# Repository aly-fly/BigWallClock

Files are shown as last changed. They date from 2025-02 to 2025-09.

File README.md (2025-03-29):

# Big Wall Clock
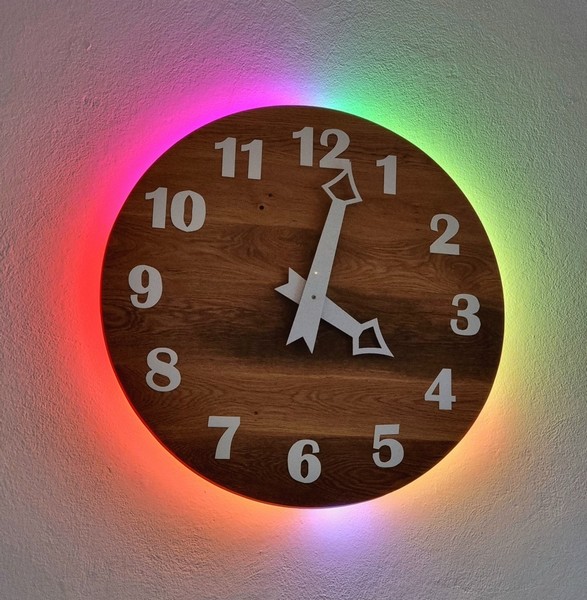
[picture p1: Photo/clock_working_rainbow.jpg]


### Story time.
_I was walking through the hardware store with my wife. High up on the wall was a huge, beautiful wooden clock. Like one meter diameter. Price tag was also pretty high. I said "I can make one like this." My brain immediately started adding features and making improvements. When the permission was given to kick-off the project, I was happy!_

## What we need

* Wooden plate
* Mechanism
* Feedback device
* Motor and driver
* Controller
* Clock hands and numbers
* Power supply

### Wooden plate
If you don't have a relative or friend that has a woodworking shop, best next option is a local furniture producer. Or recycle some other furniture with nice looking patterns.

### Mechanism
Clock with 1 meter diameter needs big and heavy clock hands. Standard off-the-shelf driving mechanism is not strong enough, and it also doesn't offer much challenges. 
Having a 3D printer in my workshop and with lots of initiative to learn mechanical design, I downloaded Autodesk Fusion Personal and started learning. Produced design is not optimal, but works pretty well. For the next iteration (if it ever comes up) one more gear after the motor is needed to increase the torque. Everything is printed from PLA, as it is hard enough so that gears should last quite some time. PETG was an alternative, as it has better dimensional tolerances and better endurance, but for now it was not needed. 

Images: ´3D_Design >> images´

Complete 3D project (Step file): ´3D_Design >> project´

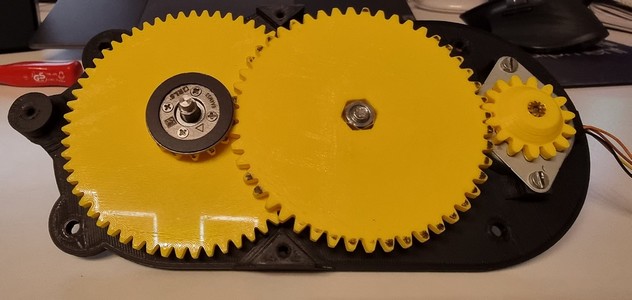
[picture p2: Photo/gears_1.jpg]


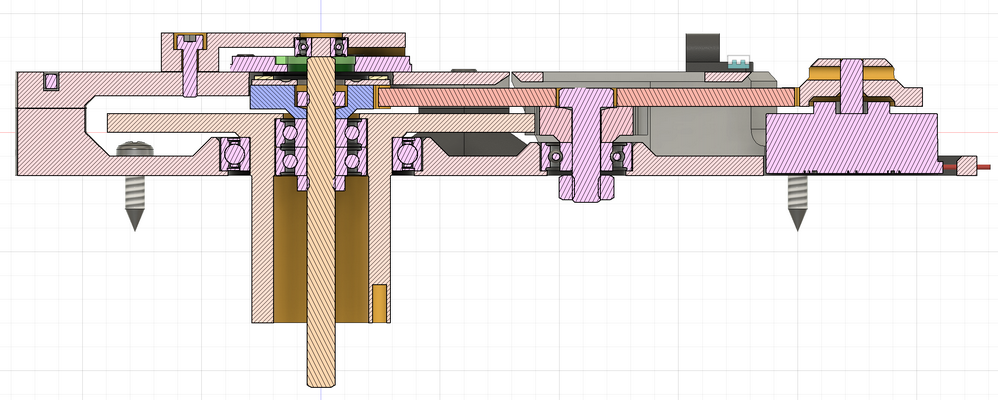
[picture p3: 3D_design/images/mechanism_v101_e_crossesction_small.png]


### Feedback device
Main idea is that clock adjusts itself to the correct time, and also takes care of the Daylight Savings time changes. For this it is required to know exact position of the clock hands. As an engineer developing the rotary encoders, my first thought was which part from our portfolio would fit. [AksIM-2](https://www.rls.si/eng/aksim-2-off-axis-rotary-absolute-encoder) with 29 mm diameter was a perfect fit. With 17-bit resolution this gives more than 2000 counts between two neighboring minute marks on the clock face. A bit too much isn't it :) But this can be used to make a very smooth and precise time-keeping. As encoder has RS422 differential output, a line-driver is required to convert signals to 3.3V LVTTL for the processor.

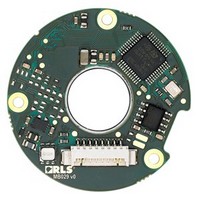
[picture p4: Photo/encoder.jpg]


### Motor and driver
With very low space available, the only motor that would fit was some thin stepper. AliExpress delivered again. Two variants were ordered, first one with 90 steps didn't have enough torque, so slightly thicker motor with better precision and better build quality was a good candidate. [0.9 Degree Mini 36mm Round Thin Stepper Motor](https://www.aliexpress.com/item/1005008263498118.html)

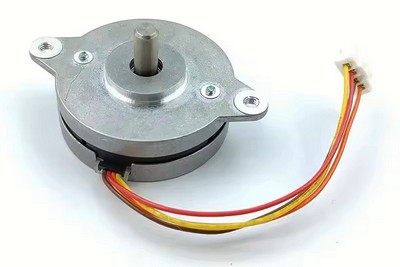
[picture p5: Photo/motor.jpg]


Having a stepper driver at hand from some other project was beneficial. ST-Spin family has some really great devices. [PowerStep01](https://www.st.com/en/motor-drivers/powerstep01.html) chip is way too powerful for what is needed here, but pure sine wave driver with 128-microstepping and quiet voltage mode really makes difference in this project.

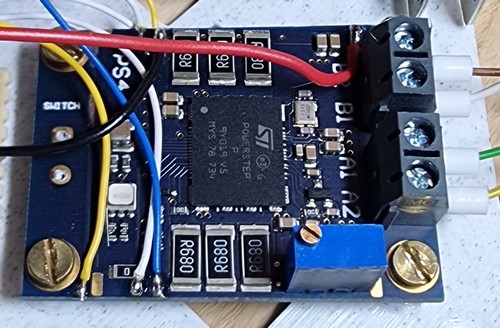
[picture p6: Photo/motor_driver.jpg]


### Controller
The programming work starts here. We need something easy to use, powerful, with lots of peripherals and of course Wi-Fi connectivity. ESP32 series is an easy choice. 
* Wi-Fi is used to get current time from the NTP server
* MQTT client talks to the Home Assistant
* UART polls data from the encoder
* SPI Sends commands to the motor driver
* ADC reads the temperature sensor of the motor
* RMT peripheral controls the addressable LED strip
* Flash filesystem is used to store system messages for later review

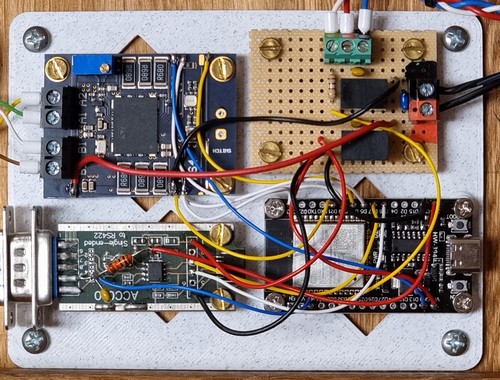
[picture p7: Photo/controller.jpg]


### Clock hands and numbers
Everything designed in Autodesk Fusion Personal and printed from PLA or PETG. 

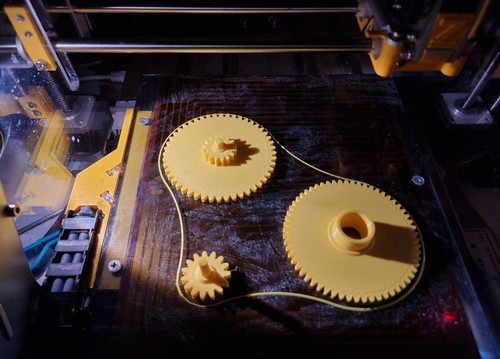
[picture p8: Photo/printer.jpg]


### LED strip
120 LEDs is a nice number to have one pixel per minute plus one in between. 60 LEDs per meter is a good choice for nice and uniform colors. The Chinese guys [delivered again](https://www.aliexpress.com/item/1005006838558445.html). LED strip is mounted using custom brackets, as can be seen in the folder ´3D_Design >> images´

### Power supply
Such a project can't be battery powered. A standard 24 V, 1 A, wall-plug supply works well. 24 V is for the motor driver. 
- Traco power [TSR 1-2450](https://www.tracopower.com/int/model/tsr-1-2450) powers the ESP32 board and encoder (1A limit).
- Traco power [TSR 3-24150](https://www.tracopower.com/int/series/tsr-3) powers the LED strip (3A limit).

## Everything mounted and tested
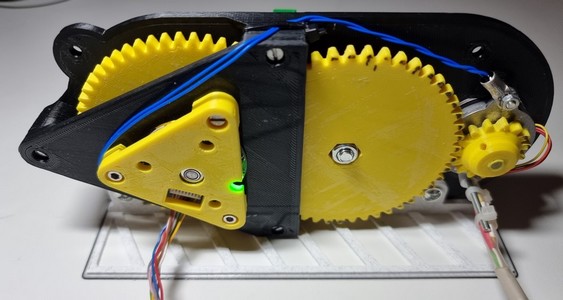
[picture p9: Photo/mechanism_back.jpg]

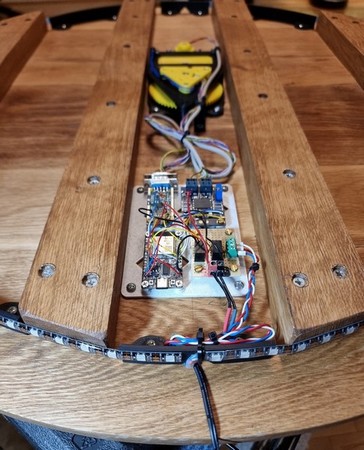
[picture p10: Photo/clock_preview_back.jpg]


### And final step is HA integration
And then the family starts enjoying the new decoration in the house.

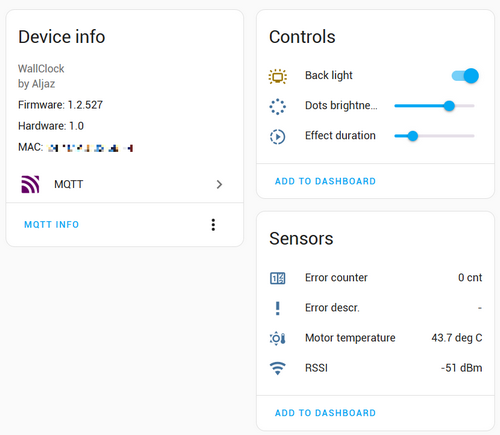
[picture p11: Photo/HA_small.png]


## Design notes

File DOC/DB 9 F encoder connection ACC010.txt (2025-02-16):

DB 9 female

  pin 1
+----------------------------+
 \  00  grn  yel  gry  brn  /
  \   red  blu  pnk  wht   /
   +----------------------+

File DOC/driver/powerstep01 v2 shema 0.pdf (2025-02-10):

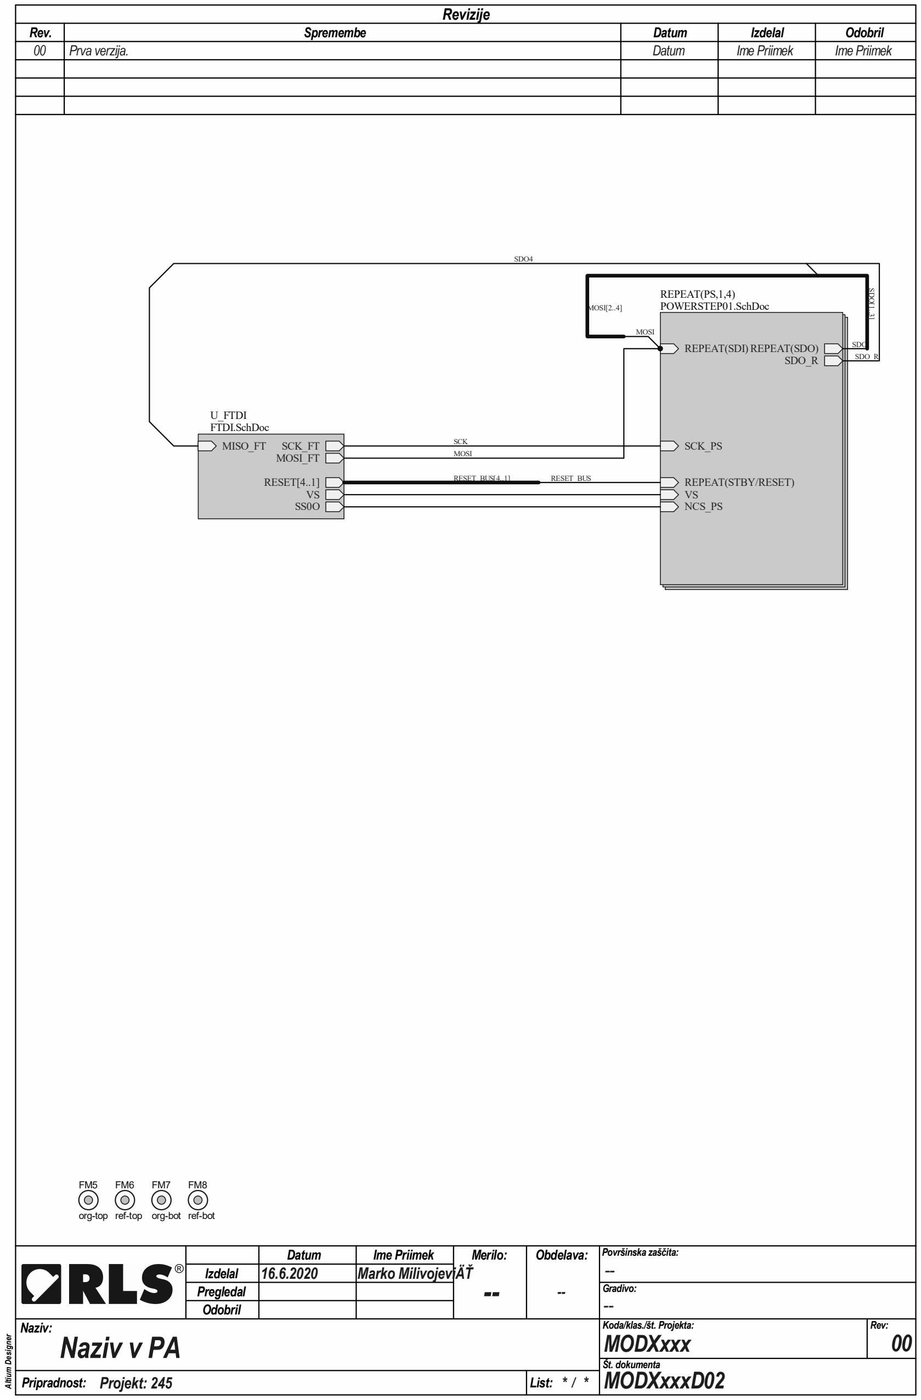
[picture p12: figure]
Rev.; Spremembe; Datum; Izdelal; Odobril; Revizije Altium Designer; 16.6.2020 Marko MilivojeviÄŤ; Pregledal; Gradivo: --; Pripradnost:; List:; Št. dokumenta; Projekt: 245; MODXxxxD02; org-top; ref-top; org-bot; ref-bot; RESET_BUS[4..1]; RESET_BUS; MOSI; SCK; SCK_PS; REPEAT(SDI)REPEAT(SDO); REPEAT(STBY/RESET) VS NCS_PS; SDO_R; REPEAT(PS,1,4); MOSI[2..4]; POWERSTEP01.SchDoc; SDO; SCK_FT MOSI_FT; MISO_FT; RESET[4..1]; U_FTDI FTDI.SchDoc; SDO4; SDO[1..3]

00 | Prva verzija. | Datum | Ime Priimek | Ime Priimek
| | Datum | Ime Priimek | Merilo: -- | Obdelava: -- | Površinska zaščita: --
Naziv: Naziv v PA | Koda/klas./št. Projekta: MODXxxx | Rev: 00

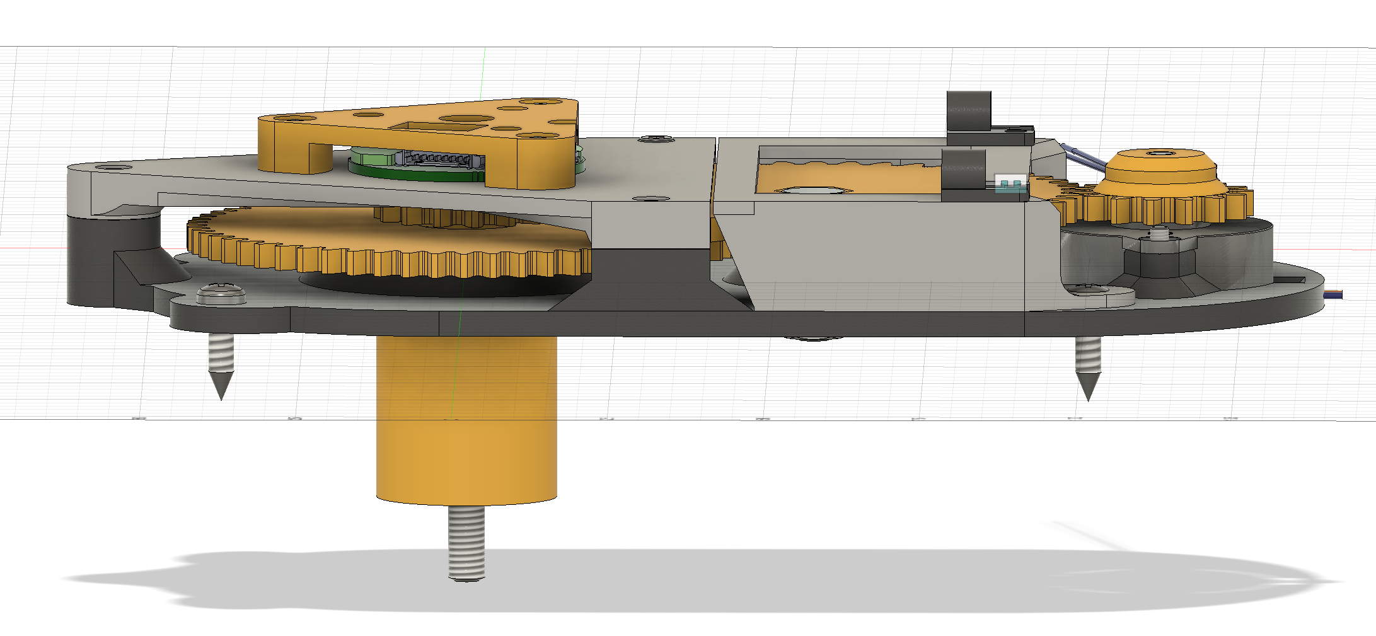
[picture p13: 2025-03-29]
3D_design/images/mechanism_v101_c.png

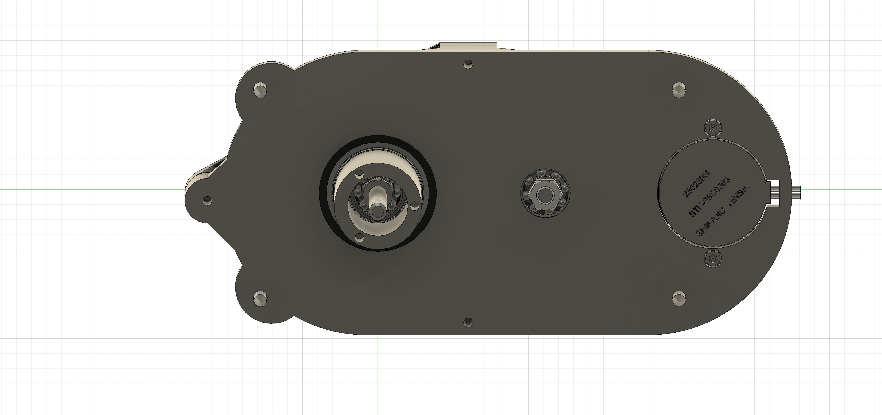
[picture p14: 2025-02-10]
3D_design/DOC/pogonski mehanizem v96 e.png

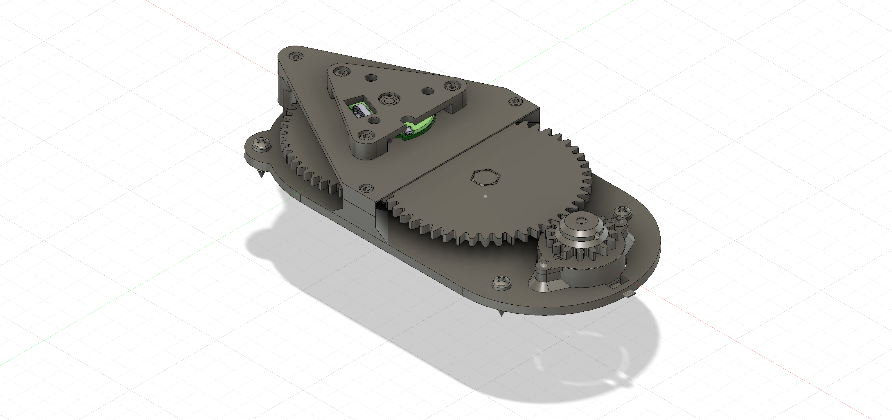
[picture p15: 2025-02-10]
3D_design/DOC/pogonski mehanizem v96 b.png

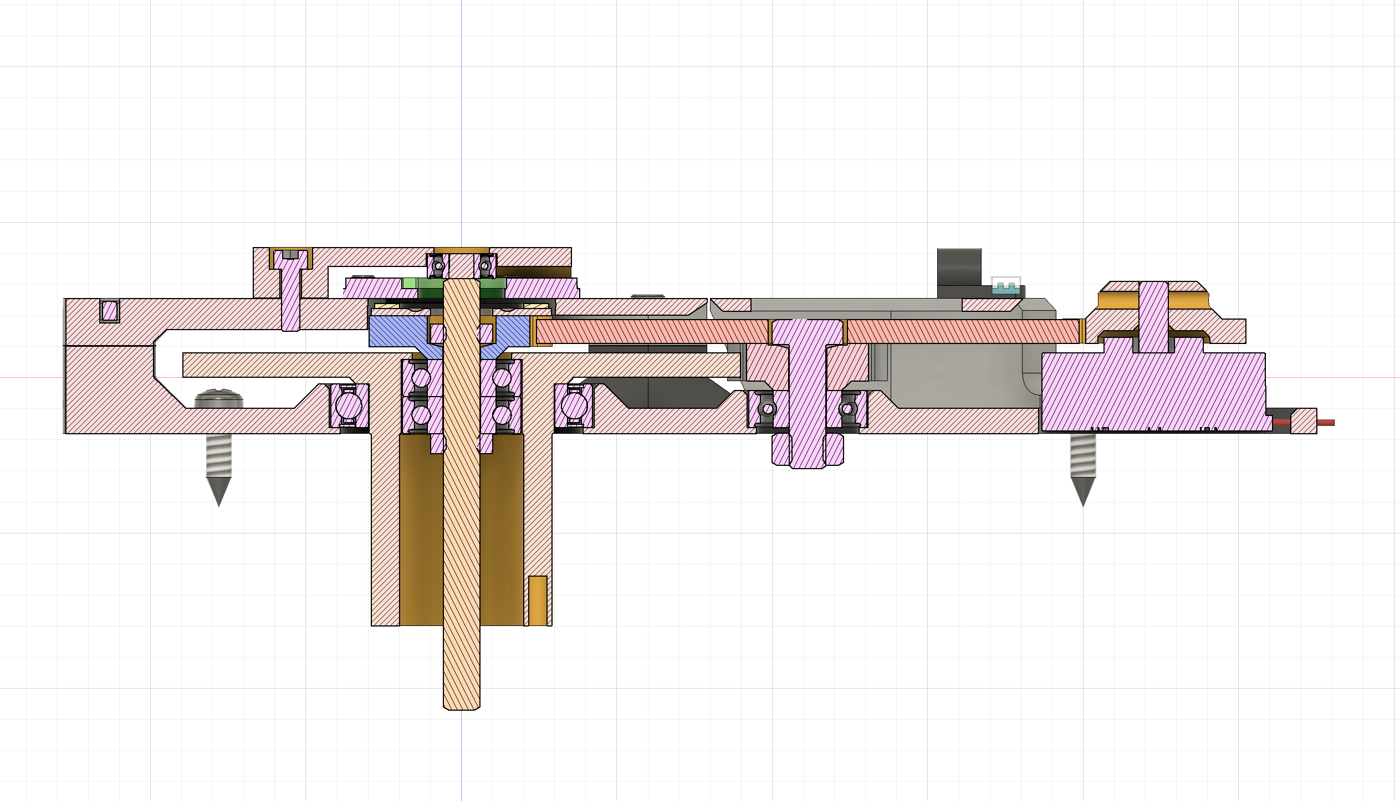
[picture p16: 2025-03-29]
3D_design/images/mechanism_v101_e_crossesction.png

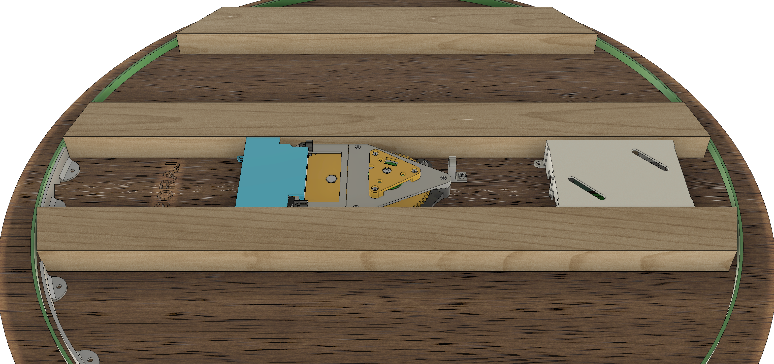
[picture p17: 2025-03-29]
3D_design/images/back_view_1.png

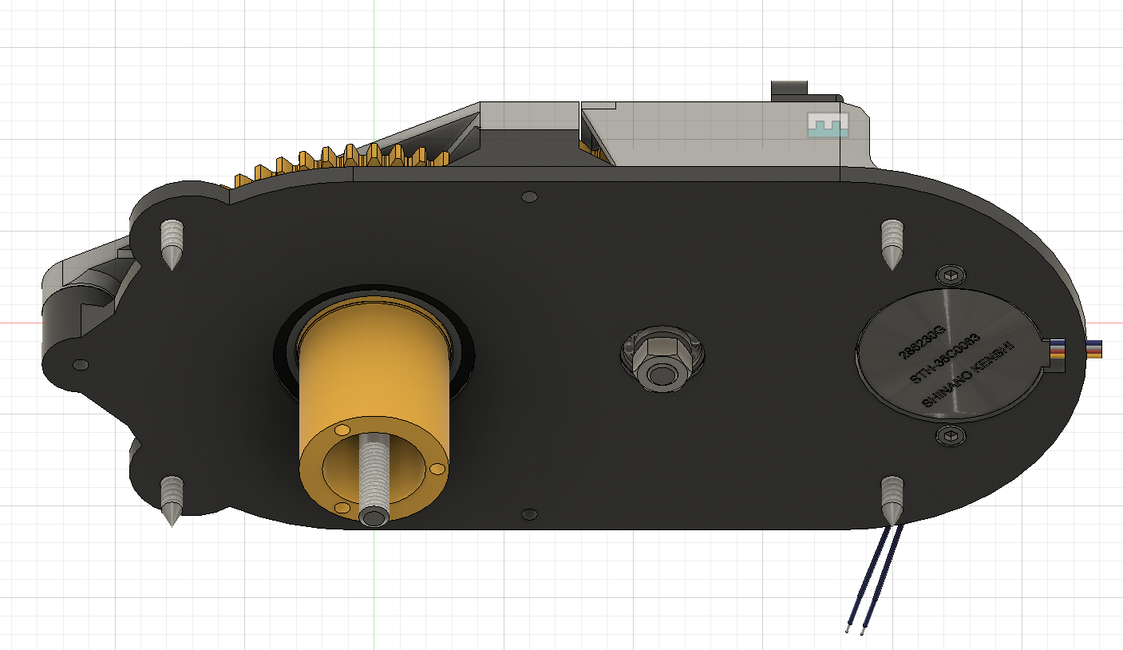
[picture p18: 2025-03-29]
3D_design/images/mechanism_v101_b.png

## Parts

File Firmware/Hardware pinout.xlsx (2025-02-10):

No. | Name | Type | GPIO | True GPIO | RTC_GPIO | ADC | TOUCH | DAC | I2C | VSPI | HSPI | SD/SDIO/MMC Host Controller | UART | Parallel QSPI | JTAG | SDIO Slave | Ethernet | Comment | USED
25 | IO00 | I/O | GPIO00 | No | RTC_GPIO11 | ADC2_CH01 | TOUCH1 |  |  |  |  |  |  |  |  |  | EMAC_TX_CLK | Low for flashing | Flashing
35 | TXD0 | I/O | GPIO01 | No |  |  |  |  |  |  |  |  | U0TXD |  |  |  | EMAC_RXD2 | Bootloader | Flashing, debug
24 | IO02 | I/O | GPIO02 | No | RTC_GPIO12 | ADC2_CH02 | TOUCH2 |  |  |  |  | HS2_DATA0 |  | HSPIWP |  |  |  | Floating or low for flashing | Flashing
34 | RXD0 | I/O | GPIO03 | No |  |  |  |  |  |  |  |  | U0RXD |  |  |  |  | Bootloader | Flashing, debug
26 | IO04 | I/O | GPIO04 |  | RTC_GPIO10 | ADC2_CH0 | TOUCH0 |  |  |  |  | HS2_DATA1 |  | HSPIHD |  |  | EMAC_TX_ER
29 | IO05 | I/O | GPIO05 |  |  |  |  |  |  | SS/CS |  | HS1_DATA6 |  | VSPICS0 |  |  | EMAC_RX_CLK |  | PowerStep01 motor driver VSPI
20 | SCK/CLK* | I/O | GPIO06 | No | UNUSABLE !!! (Flash memory) |  |  |  |  |  |  | HS1_CLK | U1CTS | SPICLK |  | SD_CLK
21 | SDO/SD0* | I/O | GPIO07 | No | UNUSABLE !!! (Flash memory) |  |  |  |  |  |  | HS1_DATA0 | U2RTS | SPIQ |  | SD_DATA0
22 | SDI/SD1* | I/O | GPIO08 | No | UNUSABLE !!! (Flash memory) |  |  |  |  |  |  | HS1_DATA1 | U2CTS | SPID |  | SD_DATA1
17 | SHD/SD2* | I/O | GPIO09 | No | UNUSABLE !!! (Flash memory) |  |  |  |  |  |  | HS1_DATA2 | U1RXD | SPIHD |  | SD_DATA2
18 | SWP/SD3* | I/O | GPIO10 | No | UNUSABLE !!! (Flash memory) |  |  |  |  |  |  | HS1_DATA3 | U1TXD | SPIWP |  | SD_DATA3
19 | SCS/CMD* | I/O | GPIO11 | No | UNUSABLE !!! (Flash memory) |  |  |  |  |  |  | HS1_CMD | U1RTS | SPICS0
14 | IO12 | I/O | GPIO12 | No | RTC_GPIO15 | ADC2_CH05 | TOUCH5 |  |  |  |  | HS2_DATA2 |  | HSPIQ | MTDI |  | EMAC_TXD3 | LOW during boot!
16 | IO13 | I/O | GPIO13 |  | RTC_GPIO14 | ADC2_CH04 | TOUCH4 |  |  |  |  | HS2_DATA3 |  | HSPID | MTCK |  | EMAC_RX_ER
13 | IO14 | I/O | GPIO14 |  | RTC_GPIO16 | ADC2_CH06 | TOUCH6 |  |  |  |  | HS2_CLK |  | HSPICLK | MTMS |  | EMAC_TXD2
23 | IO15 | I/O | GPIO15 |  | RTC_GPIO13 | ADC2_CH03 | TOUCH3 |  |  |  |  | HS2_CMD |  | HSPICS0 | MTDO |  | EMAC_RXD3 | Prevents startup log
27 | IO16 | I/O | GPIO16 |  |  |  |  |  |  |  |  | HS1_DATA4 | U2RXD |  |  |  | EMAC_CLK_OUT |  | Encoder DATA
28 | IO17 | I/O | GPIO17 |  |  |  |  |  |  |  |  | HS1_DATA5 | U2TXD |  |  |  | EMAC_CLK_OUT_180 |  | Encoder CMD
30 | IO18 | I/O | GPIO18 |  |  |  |  |  |  | SCLK |  | HS1_DATA7 |  | VSPICLK |  |  |  |  | PowerStep01 motor driver VSPI
31 | IO19 | I/O | GPIO19 |  |  |  |  |  |  | MISO |  |  | U0CTS | VSPIQ |  |  | EMAC_TXD0 |  | PowerStep01 motor driver VSPI
33 | IO21 | I/O | GPIO21 |  |  |  |  |  | SDA1 |  |  |  |  | VSPIHD |  |  | EMAC_TX_EN |  | PowerStep01 motor driver nReset
36 | IO22 | I/O | GPIO22 |  |  |  |  |  | SCL1 |  |  |  | U0RTS | VSPIWP |  |  | EMAC_TXD1
37 | IO23 | I/O | GPIO23 |  |  |  |  |  |  | MOSI |  | HS1_STROBE |  | VSPID |  |  |  |  | PowerStep01 motor driver VSPI
10 | IO25 | I/O | GPIO25 |  | RTC_GPIO06 | ADC2_CH08 |  | DAC_1 |  |  |  |  |  |  |  |  | EMAC_RXD0
11 | IO26 | I/O | GPIO26 |  | RTC_GPIO07 | ADC2_CH09 |  | DAC_2 |  |  |  |  |  |  |  |  | EMAC_RXD1
12 | IO27 | I/O | GPIO27 |  | RTC_GPIO17 | ADC2_CH07 | TOUCH7 |  |  |  |  |  |  |  |  |  | EMAC_RX_DV
8 | IO32 | I/O | GPIO32 |  | RTC_GPIO09 | ADC1_CH04 | TOUCH9 |  |  |  |  |  |  |  |  |  |  | XTAL_32K_P (32.768kHz oscillator input) | LED WS2812 data
9 | IO33 | I/O | GPIO33 |  | RTC_GPIO08 | ADC1_CH05 | TOUCH8 |  |  |  |  |  |  |  |  |  |  | XTAL_32K_N (32.768kHz oscillator outut)
6 | IO34 | I | GPIO34 | No | RTC_GPIO04 | ADC1_CH06 |  |  |  |  |  |  |  |  |  |  |  | No internal pullup
7 | IO35 | I | GPIO35 | No | RTC_GPIO05 | ADC1_CH07 |  |  |  |  |  |  |  |  |  |  |  | No internal pullup
4 | SENSOR_VP | I | GPIO36 | No | RTC_GPIO00 | ADC1_CH0 |  |  |  |  |  |  |  |  |  |  |  | No internal pullup
5 | SENSOR_VN | I | GPIO39 | No | RTC_GPIO03 | ADC1_CH03 |  |  |  |  |  |  |  |  |  |  |  | No internal pullup | NTC motor temperature sensor
1 | GND | PWR
2 | 3V3 | PWR
3 | EN | I
15 | GND | PWR
32 | NC | NC
38 | GND | PWR

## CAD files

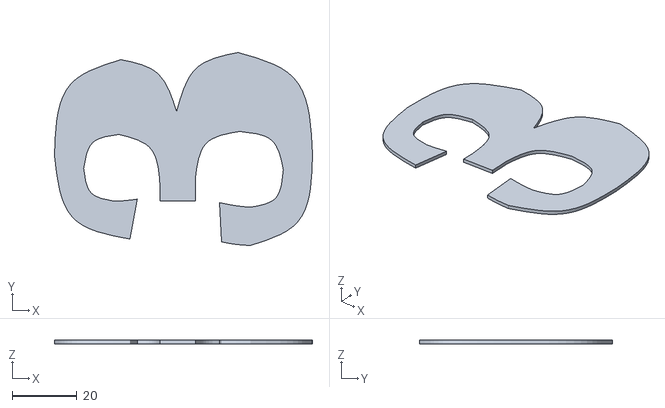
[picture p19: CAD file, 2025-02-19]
3D_design/build/Britannic Bold 77/3.stl
79.6 x 59.6 x 1.10

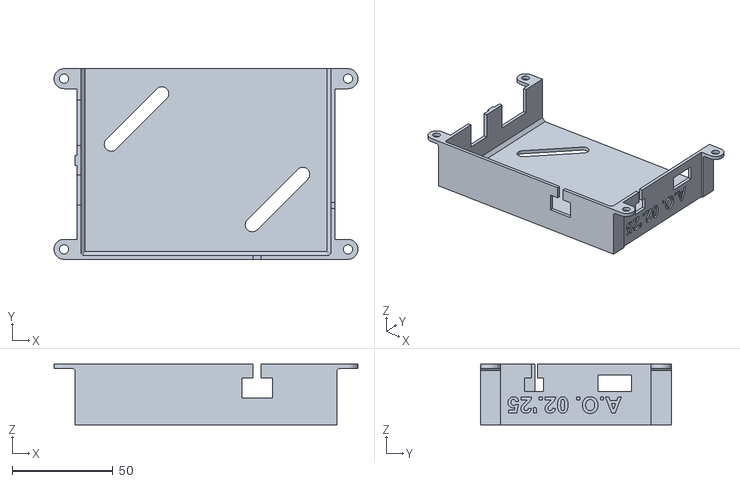
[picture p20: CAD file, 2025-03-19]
3D_design/build/pokrov elektronike 2.stl
150.9 x 94.7 x 30.1

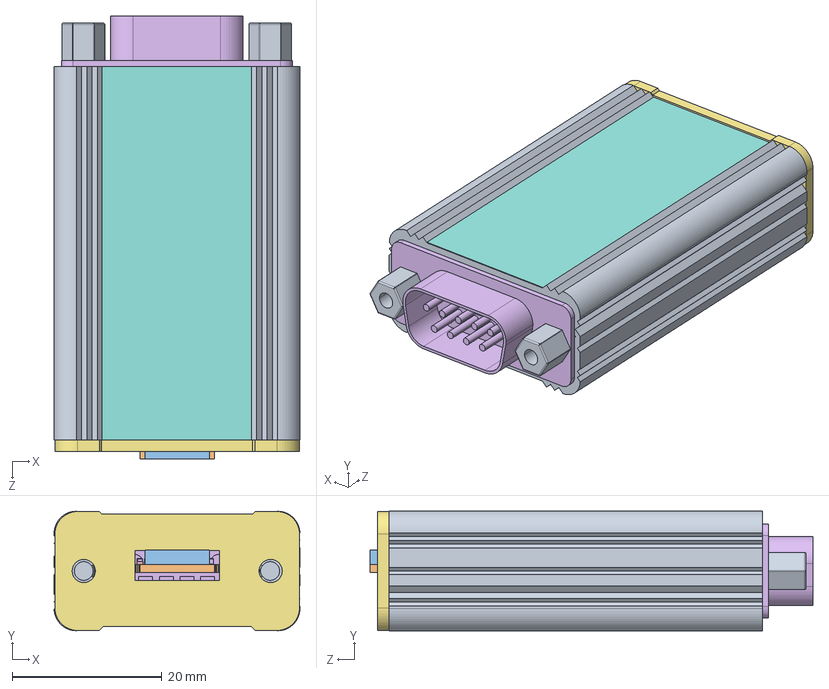
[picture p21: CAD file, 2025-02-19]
3D_design/material/LineDriver_ACC009.STEP
32.9 x 16.0 x 59.2 mm
OH33_16_v5 x 2
Board
Extruded
SW3dPS-R0805 x 3
C0603 x 6
SW3DPS-SO-8-DEFAULT
srf2012a x 2
SW3dPS-R0603 x 4
db9M_kabel
MN00909
Nalepka_50x20
distancnik_sestrobi x 2
Nalepka_s_serijsko_stevilko

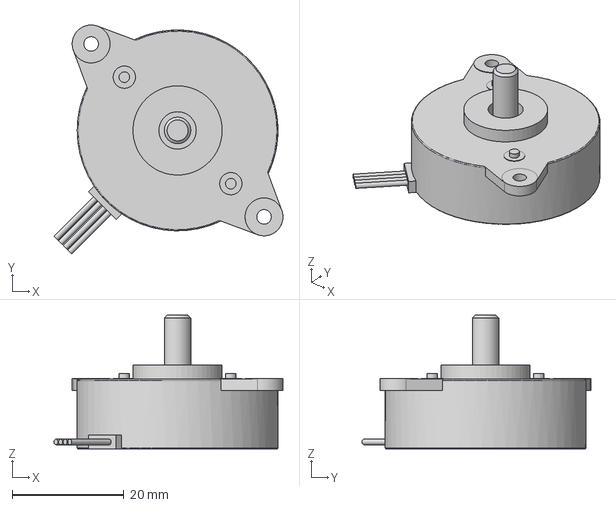
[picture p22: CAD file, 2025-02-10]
3D_design/material/motor/motor 12 mm v5.step
41.1 x 41.1 x 24.0 mm

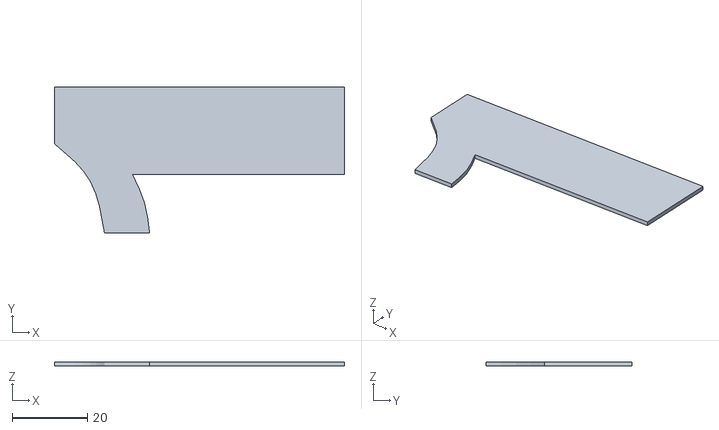
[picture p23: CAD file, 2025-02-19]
3D_design/build/Britannic Bold 77/1.stl
77.0 x 38.9 x 1.10

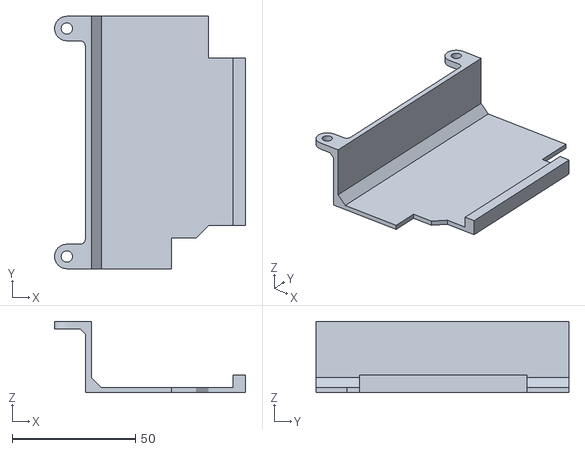
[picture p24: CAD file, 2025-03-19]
3D_design/build/dust protector 2.stl
77.5 x 102.5 x 29.0

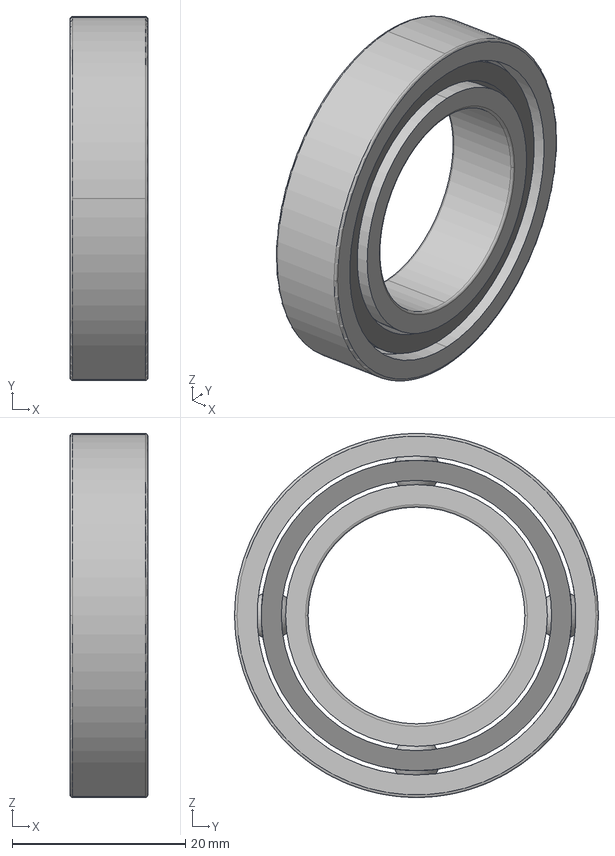
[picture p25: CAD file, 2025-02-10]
3D_design/material/bearing 61905.stp
9.00 x 42.0 x 42.0 mm

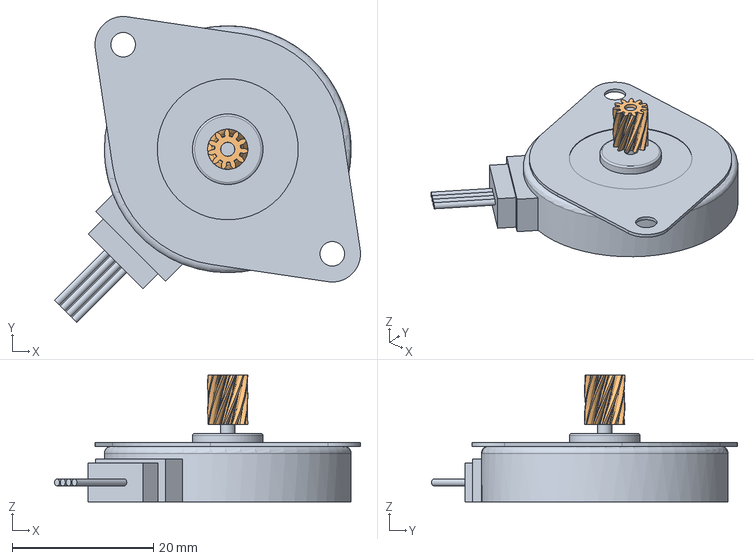
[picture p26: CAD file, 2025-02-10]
3D_design/material/motor/motor 8.4 mm v14.step
43.4 x 43.4 x 18.0 mm

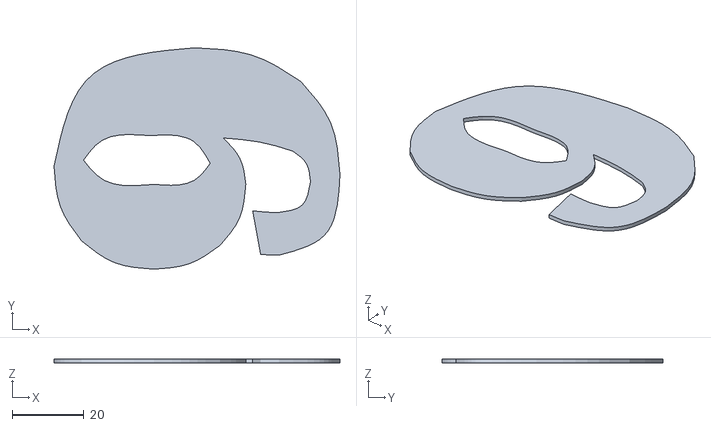
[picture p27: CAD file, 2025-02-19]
3D_design/build/Britannic Bold 77/9.stl
79.6 x 61.6 x 1.10

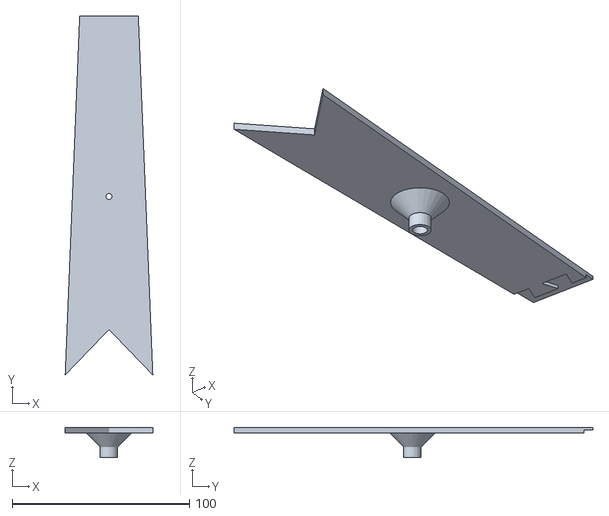
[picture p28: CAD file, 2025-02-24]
3D_design/build/hand 1 M a v61.stl
49.5 x 202.7 x 17.1

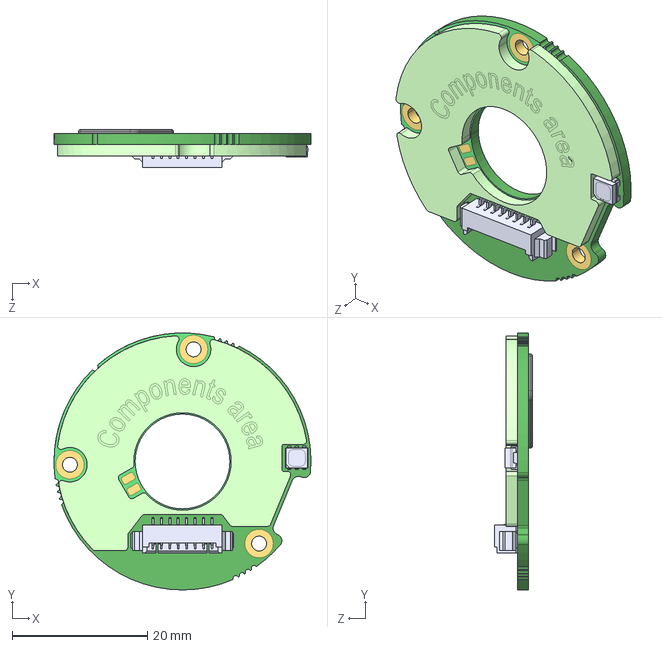
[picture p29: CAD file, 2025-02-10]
3D_design/material/MB029xxxxxxFNx00.STEP
38.0 x 38.0 x 5.68 mm

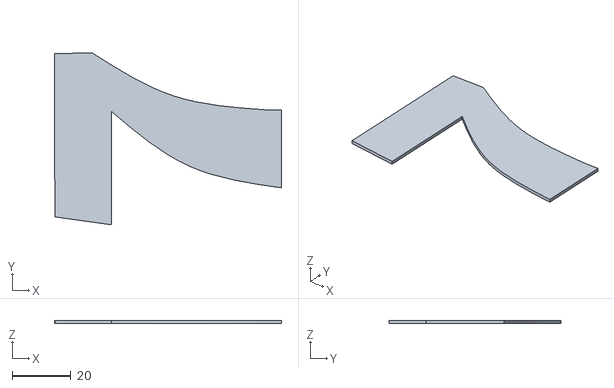
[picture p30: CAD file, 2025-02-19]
3D_design/build/Britannic Bold 77/7.stl
77.1 x 58.3 x 1.10

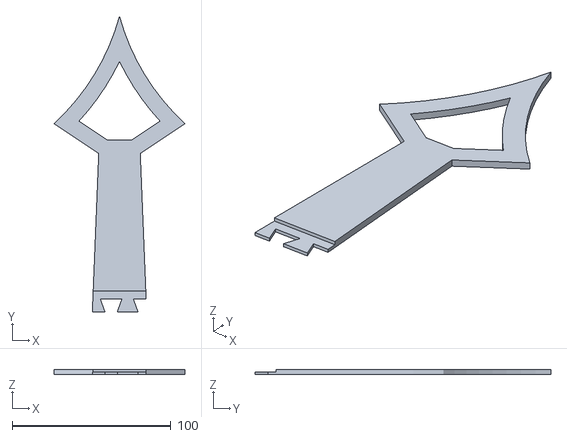
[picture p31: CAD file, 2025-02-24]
3D_design/build/hand 1 M b v61.stl
82.4 x 186.0 x 3.10

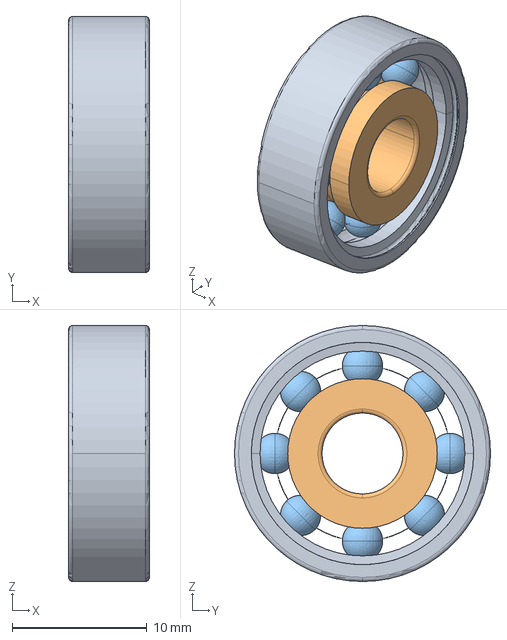
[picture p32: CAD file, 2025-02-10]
3D_design/material/bearing 626.stp
6.00 x 19.0 x 19.0 mm

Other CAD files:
3D_design/build/Britannic Bold 77/0.stl
3D_design/build/dust protector.stl
3D_design/material/adapter lager.stl
3D_design/build/Britannic Bold 77/6.stl
3D_design/build/Britannic Bold 77/2.stl
3D_design/build/Britannic Bold 77/4.stl
3D_design/build/Britannic Bold 77/5.stl
3D_design/build/Britannic Bold 77/8.stl
3D_design/build/bottom plate v93.3mf
3D_design/build/bottom plate v93.stl
3D_design/build/cover 1 encoder v54.3mf
3D_design/build/cover 1 encoder v54.stl
3D_design/build/cover 2 bearing v67.3mf
3D_design/build/cover 2 bearing v67.stl
3D_design/build/drzalo za kabel D v9.stl
3D_design/build/drzalo za kabel L v9.stl
3D_design/build/drzalo za oba kabla v4.stl
3D_design/build/gear 15 encoder v45.3mf
3D_design/build/gear 15 encoder v45.stl
3D_design/build/gear 15 motor v87.stl
3D_design/build/gear 48+16 v71.3mf
3D_design/build/gear 48+16 v71.stl
3D_design/build/gear 60 v63.3mf
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

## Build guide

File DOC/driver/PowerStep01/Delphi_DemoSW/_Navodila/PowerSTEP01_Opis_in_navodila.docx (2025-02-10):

Ukaz preko odložišča:

Format: UkazZaStepDrive( UKAZ_S_PARAMETRI )

Ko se na odložišču pojavi tekst v tem formatu, se izvede ukaz. V primeru, da se pričakuje odgovor na ukaz, se odgovor doda na koncu teksta v odložišču.

Ukaz preko ComPorta:

Format : UKAZ_S_PARAMETRI

Na PC je potrebno namestiti com0com gonilnike, ki naredijo programsko simulacjo COM portov. COM porti se dodajajo v parih, komunikacija poteka znotraj vsakega para. StepDrive aplikacija izpiše ime COM porta, ki ga je potrebno uporabiti za komunikacijo.

Ko se na ustrezen COM port pošlje veljaven ukaz, se ukaz izvrši. Če se pričakuje odgovor na ukaz, se udgovor pojavi na COM Portu.

Struktura ukaza s parametri:

UKAZ_S_PARAMETRI => Ukaz ; ŠtevilkaMotorja ; ParameterUkaza

Primer ukaza:

Set_MicroStep; 1; 128 - Ta ukaz pomeni, da kontrolerju št.1 nastavi število mikro-korakov na vrednost 128.
Preko odložišča bi isti ukaz bil: UkazZaStepDrive(Set_MicroStep; 1; 128 )

Ukazi:

- LoadConfiguration_FromFile;m;Path –> Opozorilo
  - Naloži konfiguracijo iz datoteke, ki je predpisana s paramerom Path. Ko se parametri naložijo, izbriše tudi statuse. Če datoteka ne obstaja, vrne obvestilo »Datoteka ne obstaja«.
- Run_WithSpeed; m; Hitrost -> Hitrost
  - Požene motor z ustrezno hitrostjo. Hitrost je predznačeno racionalno število, enote za hitrost so [koraki/s]. Koraki so polni koraki koračnega motorja. Vrne dejansko nastavljeno hitrost. Med pospeševanjem je vklopljen status »Busy«, ukaz se lahko da kadarkoli in se takoj izvede.
- Move_For; m; Premik -> Premik
  - Premakne motor za ustrezno število mikro-korakov. Premik je predznačen in celoštevilčen. Absolutni premik je odvisen od nastavitve števila mikro-korakov na korak. Med premikanjem je vklopljen status »Busy«, pred ukazom mora motor mirovati, največji možen premik je 4194303.
- GoTo_Short; m; Pozicija -> Pozicija
  - Pošlje motor s pospeškom in izbrano maksimalno hitrostjo na zahtevano pozicijo po najkrajši poti, pozicija je v mikro-korakih v območju +/- 2097151. Med premikanjem je vklopljen status »Busy«.
- GoTo_DirPos; m; Pozicija -> Pozicija
  - Pošlje motor s pospeškom in izbrano maksimalno hitrostjo na zahtevano pozicijo. Motor zavrti v pozitivni smeri, pozicija je v mikro-korakih v območju +/- 2097151. Med premikanjem je vklopljen status »Busy«, pred ukazom mora motor mirovati.
- GoTo_DirNeg; m; Pozicija -> Pozicija
  - Pošlje motor s pospeškom in izbrano maksimalno hitrostjo na zahtevano pozicijo. Motor zavrti v negativni smeri, pozicija je v mikro-korakih v območju +/- 2097151. Med premikanjem je vklopljen status »Busy«, pred ukazom mora motor mirovati.
- Stop_Hard; m
  - Ustavi motor takoj. Ko se motor ustavi, pusti izhodno stopnjo prižgano.
- Stop_Soft; m
  - Ustavi motor s prednastavljenim pojemkom. Ko se motor ustavi, pusti izhodno stopnjo prižgano.
- DriverHiZ; m
  - Izklopi izhodno stopnjo, posledično se ustavi vrtenje.
- GetClear_Status; m -> Status
  - Prebere statusni register in vrne njegovo vrednost. Po branju izbriše statuse, Interpretacija statusnega registra je v podatkovnem listu.
- Get_Status; m -> Status
  - Prebere statusni register in vrne njegovo vrednost. Interpretacija statusnega registra je v podatkovnem listu.
- Set_Position; m; Pozicija -> Pozicija
  - Nastavi števec pozicije na željeno vrednost, vrne nastavljeno vrednost. Ukaz se izvede, če se motor ne premika.
- Set_MarkPosition; m; Mark -> Mark
  - Nastavi »Mark« register na željeno vrednost, vrne nastavljeno vrednost. Ukaz se vedno izvede.
- Set_Acceleration; m; Pospešek -> Pospešek
  - Nastavi pospešek na željeno vrednost, enote so [korak/s²]. Vrne nastavljeno vrednost.
- Set_Deceleration; m; Pojemek -> Pojemek
  - Nastavi pojemek na željeno vrednost, enote so [korak/s²]. Vrne nastavljeno vrednost.
- Set_MaxSpeed; m; Hitrost -> Hitrost
  - Nastavi vrednost največje hitrosti, enota je [korak/s], vrne nastavljeno vrednost.
- Set_MinSpeed; m; Hitrost -> Hitrost
  - Nastavi vrednost najmanjše hitrosti, enota je [korak/s], vrne nastavljeno vrednost.
- Set_HoldCurrent; m; Tok -> Tok
  - Nastavi tok, ki naj teče med mirovanjem, enote so [mA], vrne nastavljeno vrednost.
- Set_RunCurrent; m, Tok -> Tok
  - Nastavi tok, ki naj teče med premikanjem s stalno hitrostjo, enote so [mA], vrne nastavljeno vrednost.
- Set_AccCurrent; m; Tok -> Tok
  - Nastavi tok, ki naj teče med pospeševanjem, enote so [mA], vrne nastavljeno vrednost.
- Set_DecCurrent; m; Tok -> Tok
  - Nastavi tok, ki naj teče med zmanjševanjem hitrosti, enote so [mA], vrne nastavljeno vrednost.
- Set_MicroStep; m; µKorak -> µKorak
  - Nastavi koliko mikro-korakov naj bo na korak. Vrne nastavljeno vrednost. Vrednost se lahko nastavlja samo, ko je izklopljena izhodna stopnja.
- Get_IsBusy; m -> Status
  - Če je vklopljen status »Busy«, vrne 1, drugače vrne 0.
- Get_IsBridgeOn; m -> Status
  - Če je izhodna stopnja vklopljena, vrne 1, drugače vrne 0.
- Get_IsCommandError; m -> Status
  - Prebere »CommandError« status. Če je bil Error, vrne 1 drugače vrne 0.
- Get_IsSwitchOn; m -> Status
  - Pogleda, če je končno stikalo sklenjeno. Če je sklenjeno, vrne 1, drugače vrne 0.
- Get_Acceleration; m
- Get_Deceleration; m
- Get_MaxSpeed; m
- Get_MinSpeed; m
- Get_Position; m
- Get_MarkPosition; m
- Get_Speed; m
- Get_HoldCurrent; m
- Get_RunCurrent; m
- Get_AccCurrent; m
- Get_DecCurrent; m
- Get_MicroStep; m
- GoToSwitch_ResetAbs_SoftStop; m // Motion with desired speed until SW closed, after event SoftStop. At SW event ABS register is reset
- GoToSwitch_AbsToMark_SoftStop ; m // Motion with desired speed until SW closed, after event SoftStop. At SW event MARK register is preset with ABS register
- ReleaseSwitch_ResetAbs; m // Motion with minimum speed until SW opened, after event HardStop. At SW event ABS register is reset
- ReleaseSwitch_AbsToMark ; m // Motion with minimum speed until SW opened, after event HardStop. At SW event MARK register is preset with ABS register

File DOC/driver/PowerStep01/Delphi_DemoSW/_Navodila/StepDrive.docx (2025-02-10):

Ftd2xx.dll

Ftd2xx.dll

FTD2xx unit

LibFT4222 unit

StSpin unit

Odložišče

Poljubna aplikacija

COM port aplikacija

Opcijsko

StepDrive
aplikacija

com0com gonilnik

Koračni motor 4

SPI

powerSTEP01

Koračni motor 3

SPI

powerSTEP01

Koračni motor 2

SPI

powerSTEP01

Koračni motor 1

SPI

powerSTEP01

SPI

Koračni motor 5

powerSTEP01

USB

FT4222

PC

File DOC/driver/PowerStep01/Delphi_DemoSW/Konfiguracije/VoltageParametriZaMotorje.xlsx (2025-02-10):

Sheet: 17HS13
Ke | 0.06
R | 30
L | 34
Nom. Tok | 0.4
Prvi parametri
Int_Spd | $2396
St_Slp | $52
Fn_Slp_Acc | $90
Fn_Slp_Dec | $90
 | 400 | 300 | 200 | 100
Tok | $7B | $5A | $3D | $1E
Int_Spd | $1000 | $1000 | $1000 | $1000
St_Slp | $2A | $27 | $23 | $22
Fn_Slp_Acc | $52 | $4A | $43 | $36
Fn_Slp_Dec | $52 | $4A | $43 | $36
Tok
Fn_Slp_Dec | 82 | 74 | 67 | 54
 | Tok | St_Slp | Fn_Slp_Acc
 | 123 | 42 | 82
 | 90 | 38 | 74
 | 61 | 35 | 67
 | 30 | 31 | 58

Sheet: 17HS15
Ke | 0.026
R | 1.65
L | 3.2
Nom. Tok | 1.68
Prvi parametri
Int_Spd | $2396
St_Slp | $52
Fn_Slp_Acc | $90
Fn_Slp_Dec | $90
 | 1712 | 1275 | 850 | 425
Tok | $23 | $18 | $11 | $08
Int_Spd | $1000 | $1000 | $1000 | $1000
St_Slp | $19 | $17 | $14 | $13
Fn_Slp_Acc | $2C | $26 | $20 | $18
Fn_Slp_Dec | $2C | $26 | $20 | $18
 | Tok | St_Slp | Fn_Slp_Acc
 | 35 | 25 | 44
 | 24 | 22 | 37
 | 17 | 20.5 | 32
 | 8 | 18.5 | 25

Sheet: 11LS18
Ke | 0.013
R | 6.7
L | 3
Nom. Tok | 0.75
Prvi parametri
Int_Spd | $3FFF
St_Slp | $11
Fn_Slp_Acc | $1F
Fn_Slp_Dec | $1F
 | 1 | 0.75 | 0.5 | 0.25
Tok | $4B | $36 | $25 | $12
Int_Spd | $2100 | $2100 | $2100 | $2100
St_Slp | $0D | $0C | $0A | $09
Fn_Slp_Acc | $18 | $12 | $0F | $0C
Fn_Slp_Dec | $18 | $12 | $0F | $0C
 | Tok | St_Slp | Fn_Slp_Acc
 | 75 | 13.5 | 22.5
 | 54 | 11.5 | 18.5
 | 37 | 10 | 15
 | 18 | 8.5 | 11.5

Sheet: SY28STH45
Ke | 0.0125
R | 6.8
L | 4.9
Nom. Tok | 0.67
Prvi parametri
Int_Spd | $39E6
St_Slp | $09
Fn_Slp_Acc | $1F
Fn_Slp_Dec | $1F
 | 1 | 0.75 | 0.5 | 0.25
Tok | $4D | $39 | $26 | $13
Int_Spd | $2800 | $2800 | $2800 | $2800
St_Slp | $0F | $0C | $0A | $09
Fn_Slp_Acc | $1F | $18 | $13 | $0E
Fn_Slp_Dec | $1F | $18 | $13 | $0E
 | Tok | St_Slp | Fn_Slp_Acc
 | 77 | 14.5 | 30
 | 57 | 12.2 | 24.4
 | 38 | 10 | 19
 | 19 | 8 | 13.8

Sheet: S20STH30
Ke | 0.03
R | 6.5
L | 1.7
Nom. Tok | 0.6
Prvi parametri
Int_Spd | $3FFF
St_Slp | $14
Fn_Slp_Acc | $1A
Fn_Slp_Dec | $1A
 | 1 | 0.75 | 0.5 | 0.25
Tok | $48 | $36 | $24 | $12
Int_Spd | $3FFF | $3FFF | $3FFF | $3FFF
St_Slp | $03 | $02 | $02 | $02
Fn_Slp_Acc | $0B | $09 | $06 | $04
Fn_Slp_Dec | $0B | $09 | $06 | $04
 | Tok | St_Slp | Fn_Slp_Acc
 | 72 | 3 | 11
 | 54 | 2 | 8.6
 | 36 | 2 | 6.2
 | 18 | 2 | 3.9

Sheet: ST4118M
Ke | 0.06
R | 3.6
L | 1.85
Nom. Tok | 1.8
Prvi parametri
Int_Spd | $3FFF
St_Slp | $29
Fn_Slp_Acc | $3A
Fn_Slp_Dec | $3A
 | 2 | 1.5 | 1 | 0.5
Tok | $53 | $3E | $29 | $14
Int_Spd | $0A00 | $0A00 | $0A00 | $0A00
St_Slp | $31 | $28 | $26 | $24
Fn_Slp_Acc | $65 | $5A | $4C | $3A
Fn_Slp_Dec | $65 | $5A | $4C | $3A
 | Tok | St_Slp | Fn_Slp_Acc
 | 83 | 49 | 102
 | 62 | 43 | 89
 | 41 | 38 | 75
 | 20 | 33 | 59

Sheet: SY42STH33-1334B
Ke | 0.0185
R | 2.1
L | 2.5
Nom. Tok | 1.33
Prvi parametri
Int_Spd | $3FFF
St_Slp | $29
Fn_Slp_Acc | $3A
Fn_Slp_Dec | $3A
 | 1.5 | 1.1 | 0.75 | 0.38
Tok | $26 | $1C | $13 | $09
Int_Spd | $1600 | $1600 | $1600 | $1600
St_Slp | $0F | $0D | $0D | $0C
Fn_Slp_Acc | $21 | $1C | $16 | $11
Fn_Slp_Dec | $21 | $1C | $16 | $11
 | Tok | St_Slp | Fn_Slp_Acc
 | 38 | 15 | 33
 | 28 | 13.7 | 27.2
 | 19 | 12.7 | 22.1
 | 9 | 11.8 | 16.8

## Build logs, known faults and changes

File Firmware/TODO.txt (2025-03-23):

- TCP server - terminal
    - log redirect 
    https://www.esp32.com/viewtopic.php?t=3960
    https://github.com/espressif/esp-idf/issues/13205
    https://docs.espressif.com/projects/esp-idf/en/stable/esp32/api-reference/system/log.html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
    https://www.google.com/search?q=esp_log_set_vprintf

- hardcoded settings moved to nvram

- MQTT integration with autodiscovery for hardcoded

- motor temperature filter

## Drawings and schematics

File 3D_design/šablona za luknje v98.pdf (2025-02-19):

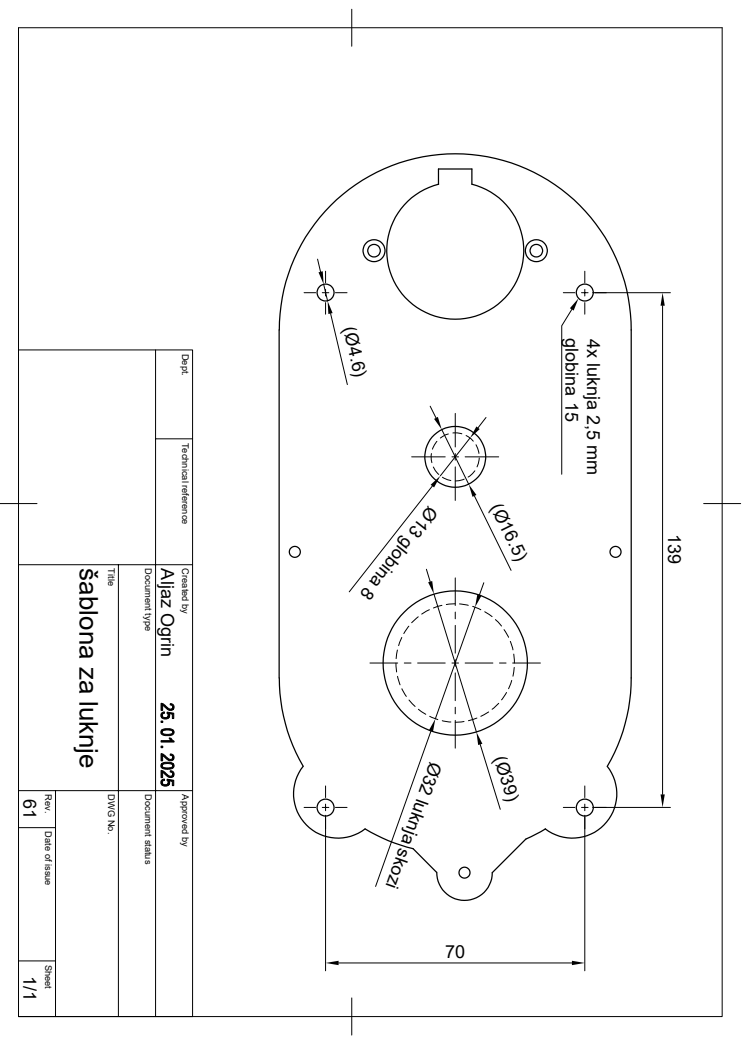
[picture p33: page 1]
Ø32 luknja skozi

(Ø39) globina 15 4x luknja 2,5 mm (Ø4.6) 139

Dept. Technical reference Created by Approved by Title DWG No. Document type Document status 61 Rev. Date of issue Sheet 1/1 šablona za luknje Aljaz Ogrin

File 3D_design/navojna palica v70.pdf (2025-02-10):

Ø4

# postruženo

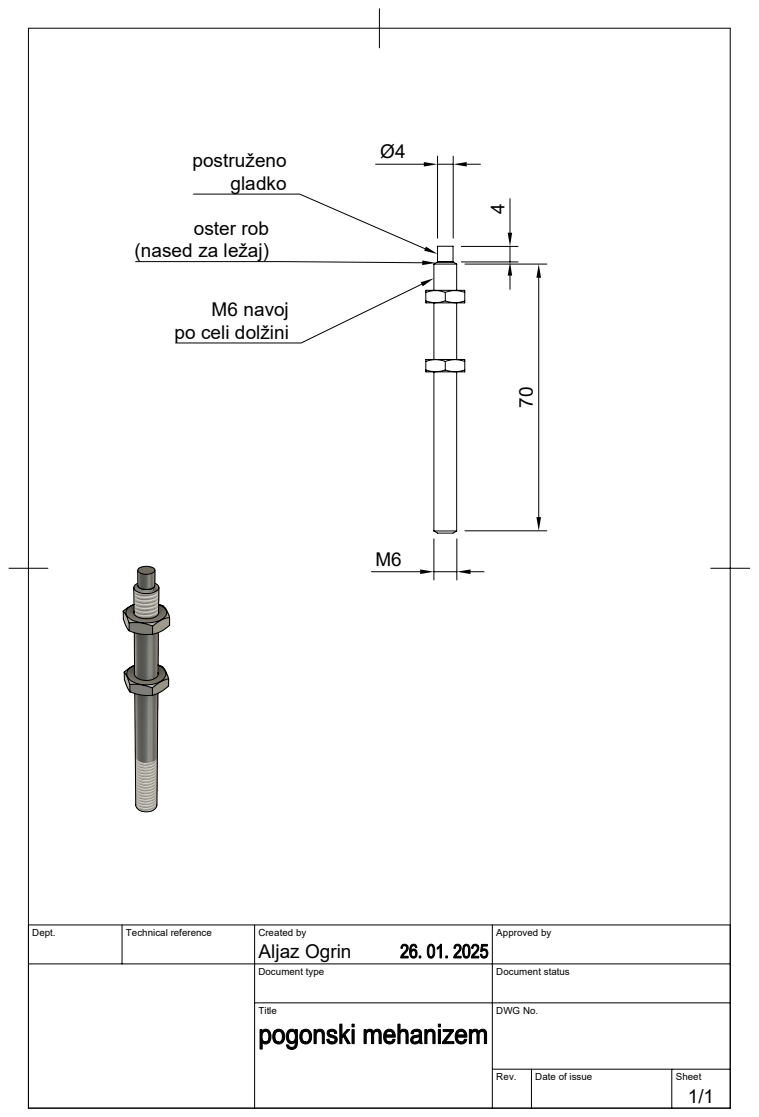
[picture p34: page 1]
Dept.; Technical reference; Created by; Approved by; Document type; Document status; Title; DWG No.; Rev.; Date of issue; Sheet; Aljaz Ogrin; gladko

oster rob
(nased za ležaj)

M6 navoj
po celi dolžini

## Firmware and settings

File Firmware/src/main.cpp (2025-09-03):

#include <Arduino.h>
#include <stdint.h>
#include <stdlib.h>
#include <SPIFFS.h>
#include "Version.h"
#include "__CONFIG.h"
#include "GlobalVariables.h"
#include "LED_builtin.h"
#include "myWiFi.h"
#include "Clock.h"
#include "myPing.h"
#include "motorDriver.h"
#include "TempSensor.h"
#include "Aksim2_encoder_uart2.h"
#include "LEDs.h"
#include "Logger.h"
#include "fileSystem.h"
#include "TcpSocket.h"
#include "OTA.h"
#include "SerialCommands.h"
#include "ResetReason.h"
#include "utils.h"
#include "NVS_storage.h"

#ifdef MQTT_ENABLED
#include "Mqtt_client_HA.h"
#endif

void MainLoopBackgroundTasks(void);

void setup()
{
  Serial.begin(115200);
  pinMode(GPIO_NUM_0, INPUT_PULLUP);
  LEDbuiltin_init();
  LEDbuiltin_ON();

  // delay 2 sec on the start to connect from programmer to serial terminal
  int i;
  for (i = 0; i < 10; i++)
  {
    Serial.print("*");
    delay(100);
  }
  Serial.println();
  Log("########################################");
  Log("Project: github.com/aly-fly/BigWallClock");
  Log("Version: %s", VERSION);
  Log("Build: %s", BUILD_TIMESTAMP);
  Serial.println(F(__FILE__ __DATE__ __TIME__));
  Log(get_reset_reason().c_str());

  LED_init();

  if (!digitalRead(GPIO_NUM_0))
  {
    LED_test();
    while (1)
      yield();
  }

  storedConfigLoad();

  uint32_t tailColor = clBLUEdim;
  LED_showProgressNumber(1, clORANGEbright, tailColor);
  if (fileSystem_init())
    LED_showProgressNumber(1, clBLUEbright, tailColor);
  else
  {
    tailColor = clREDdim;
    LED_showProgressNumber(1, clREDbright, tailColor);
  }
  delay(200);

  LED_showProgressNumber(2, clORANGEbright, tailColor);
  if (WifiInit())
    LED_showProgressNumber(2, clBLUEbright, tailColor);
  else
  {
    tailColor = clREDdim;
    LED_showProgressNumber(2, clREDbright, tailColor);
  }
  delay(200);
  startTcpSocket();
  OTA_init();

  LED_showProgressNumber(4, clORANGEbright, tailColor);
  if (encoderInit())
    LED_showProgressNumber(4, clBLUEbright, tailColor);
  else
  {
    tailColor = clREDdim;
    LED_showProgressNumber(4, clREDbright, tailColor);
    Log("ENCODER INIT FAILED. HALTED.");
    while (1) // stop here
    {
      MainLoopBackgroundTasks();
    }
  }
  delay(200);

  LED_showProgressNumber(6, clORANGEbright, tailColor);
  if (MotorInit())
    LED_showProgressNumber(6, clBLUEbright, tailColor);
  else
  {
    tailColor = clREDdim;
    LED_showProgressNumber(6, clREDbright, tailColor);
    Log("MOTOR INIT FAILED. HALTED.");
    while (1) // stop here
    {
      MainLoopBackgroundTasks();
    }
  }
  delay(200);

  LED_showProgressNumber(8, clORANGEbright, tailColor);
  if (TempSensorInit())
    LED_showProgressNumber(8, clBLUEbright, tailColor);
  else
  {
    tailColor = clREDdim;
    LED_showProgressNumber(8, clREDbright, tailColor);
    Log("TEMP SENSOR INIT FAILED. HALTED.");
    while (1) // stop here
    {
      MainLoopBackgroundTasks();
    }
  }
  delay(200);

  LED_showProgressNumber(9, clORANGEbright, tailColor);
  setClock();
  LED_showProgressNumber(9, clBLUEbright, tailColor);
  delay(300);

#ifdef MQTT_ENABLED
  LED_showProgressNumber(10, clORANGEbright, tailColor);
  Log("MQTT start...");
  if (MqttStart())
  {
    LED_showProgressNumber(10, clBLUEbright, tailColor);
    Log("MQTT start Done.");
  }
  else
  {
    tailColor = clREDdim;
    LED_showProgressNumber(10, clREDbright, tailColor);
    Log("MQTT start Error!");
  }
#endif

  EnableMotor(true);
  LED_showProgressNumber(12, clBLUEbright, tailColor);
  delay(300);

  /*
    String sPingIP;
    IPAddress pingIP;
    sPingIP = "216.58.205.46"; // google.com
    pingIP.fromString(sPingIP);
    Serial.println(sPingIP);
    int pingOk = ppiinngg(pingIP);

    if (pingOk == 0) {
      Serial.println("=== REBOOT ===");
      delay (15000);
      ESP.restart();  // retry everything from the beginning
    }
  */

  LogNS("INIT FINISHED.\r\n\r\n");
  Serial.println(SERIAL_COMMANDS_LIST); // don't send to other channels
  Log("===== Init finished. Clock running. ===== ");

  LEDbuiltin_OFF();
  LED_clear(false);
  LED_SetPixelColor(0, clGREENbright, true);
}

// ===============================================================================================================================================================

int CurrentHour12;
int delta;
float speedAdjFiltered;
bool speedFilterValid = false;
bool ErrorCounterLogged = false;

int LastHour = -1;
float MotorTemperatureFiltered = 0;
float MotorTemperature = 0;
float MotorTempLastLogged = -100;
bool tempFilterValid = false;

int heartBeatLed = 0;

unsigned long LastTimeClockTaskRun = 0;

unsigned long LastTimeLEDTaskRun = 0; // limit refresh rate

String ClockErrorText;

void MainLoopClockTasks(void)
{
  if (!HasTimeElapsed(&LastTimeClockTaskRun, 100))
    return; // run 10x per second

  ClockErrorText = "-"; // not an empty string

  ClockWarning = false;
  ClockError = false;
  delta = 0;

  if (GetCurrentTime())
  {
    if (ClockEnabled)
    {
      float speedAdj = 0;
      if (encoderRead(false)) // print only if encoder encounters an error
      {
        if (!EncoderError)
        {
          int EncoderPosMT12 = (EncoderPosMT % 12);
          int TimeDisplayed = EncoderPosST + EncoderPosMT12 * CPR; // 0...131'071 (2^17)

          CurrentHour12 = (CurrentHour % 12);
          int TimeCurrent = (CurrentHour12 * CPR) + (CurrentMinute * CPR) / 60 + ((CurrentSecond * CPR) / 60 / 60);
          if (TestMode)
            LogNS("MT12 = %d; Hr = %d; Hr12 = %d;\r\n", EncoderPosMT12, CurrentHour, CurrentHour12);

          delta = TimeCurrent - TimeDisplayed; // positive -> move forward
          // handle overflow at 0:00 and 12:00
          if (delta > CPR12half)
            delta -= CPR12;
          if (delta < -CPR12half)
            delta += CPR12;

          if (abs(delta) > ((int)CPR / 60)) // more than 1 minute off
          {
            ErrorCounter += 2;
            // ClockErrorText.concat("OneMinDiff ");
          }

          speedAdj = (float)delta / 600; // P regulator

          // low-pass filter for small movements
          if ((abs(speedAdj) > 2) || (!speedFilterValid))
          {
            speedAdjFiltered = speedAdj; // pass through - no filter
            speedFilterValid = true;
          }
          else
          {
            speedAdjFiltered = (speedAdj * 0.05) + (speedAdjFiltered * 0.95);
          }
          if (TestMode)
            LogNS("Encoder = %d; Time = %d; delta = %d; speedAdj = %f; Filtered = %f\r\n", TimeDisplayed, TimeCurrent, delta, speedAdj, speedAdjFiltered);

        } // encoder no error
        else
        { // encoder error
          speedFilterValid = false;
          ClockError = true;
          ClockErrorText.concat("EncoderError ");
        }

        if ((EncoderPosMT == 12) && (EncoderPosST > 100))
        {
          LogNS("Clock is at 12:00 -> Reset MT to 0...\r\n");
          EncoderSetMT(0);
        }
        if (EncoderWarning)
        {
          ClockWarning = true;
          ClockErrorText.concat("EncoderWarning ");
        }
      } // encoder read ok
      else
      { // reading encoder failed
        speedFilterValid = false;
        ClockError = true;
        ClockErrorText.concat("EncoderReadErr ");
      }

      // 400 steps = 1 hour = 60 min = 3600 s
      // speed = 400 steps / 3600 s = 0.11111 step / s
      float speedMotor = 0.11111111;

      if (abs(speedAdj) > 0.05) // ignore very tiny corrections
      {
        speedMotor += speedAdjFiltered;
      }

      MoveConstSpeed(speedMotor); // constant movement + corrections
    } // clock enabled
    else
    {
      speedFilterValid = false;
      if (encoderRead(false)) // print only if encoder encounters an error
        if ((EncoderPosMT == 12) && (EncoderPosST > 100))
        {
          LogNS("Clock is at 12:00 -> Reset MT to 0...\r\n");
          EncoderSetMT(0);
        }
    } // clock not enabled
  } // get time
  else
  {
    Log("Getting current time failed!");
    ClockErrorText.concat("GetTimeFail ");
    ClockError = true;
  }

  motorStatus_t motSta = MotorGetStatus();
  if (motSta == MSFAULT)
  {
    Log("Motor failure!");
    ClockErrorText.concat("MotorFail ");
    ErrorCounter = 4000;
    ClockError = true;
    // disable immediatelly
    EnableMotor(false);
    ClockEnabled = false;
  }
  if (motSta == MSSTALL)
  {
    Log("Stall detected. Moving backwards a bit.");
    ClockErrorText.concat("MotorStall ");
    ErrorCounter += 50;
    MoveConstSpeed(-SPEED_LIMIT); // max speed reverse
    delay(500);
    MoveConstSpeed(+SPEED_LIMIT); // max speed forward
    delay(600);
    speedFilterValid = false;
  }

  float MotorTemperatureRaw = TempSensorRead();

  // low-pass filter
  if ((abs(MotorTemperatureRaw - MotorTemperatureFiltered) > 10) || (!tempFilterValid))
  {
    MotorTemperatureFiltered = MotorTemperatureRaw; // pass through - no filter
    tempFilterValid = true;
  }
  else
  {
    MotorTemperatureFiltered = (MotorTemperatureRaw * 0.03) + (MotorTemperatureFiltered * 0.97);
  }

  MotorTemperature = roundToOneDecimal(MotorTemperatureFiltered);

  if (abs(MotorTempLastLogged - MotorTemperature) > 4)
  {
    Log("Motor temperature = %.1f C", MotorTemperature);
    MotorTempLastLogged = MotorTemperature;
  }
  if (MotorTemperature > (MOTOR_TEMP_MAX + 5))
  {
    Log("Motor too hot! Temperature = %.1f C", MotorTemperature);
    ClockErrorText.concat("MotorTooHot ");
    ErrorCounter = 4000;
    ClockError = true;
    // disable immediatelly
    EnableMotor(false);
    ClockEnabled = false;
  }
  else if (MotorTemperature > MOTOR_TEMP_MAX)
  {
    Log("Motor overheating! Temperature = %.1f C", MotorTemperature);
    ClockErrorText.concat("MotorHot ");
    ErrorCounter += 30;
    ClockWarning = true;
  }
  if (MotorTemperature < 10)
  {
    Log("Reading motor temperature failed! Temperature = %.1f C", MotorTemperature);
    ClockErrorText.concat("TempSensorFail ");
    ErrorCounter = 4000;
    ClockError = true;
  }

  //========================================================================================================

  if (ErrorCounter > 0x00FFFFFF)
    ErrorCounter = 0x00FFFFFF;
  ErrorCounter--;
  if (ErrorCounter < 0)
    ErrorCounter = 0;
  if ((ErrorCounter > 20) && (!ErrorCounterLogged))
  {
//  Log("ErrorCounter increasing! (diff = %.2f min) ", (float)delta * 60 / CPR);
    Log("ErrorCounter increasing!");
    encoderRead(true); // log position
    ErrorCounterLogged = true;
  }
  if ((ErrorCounter == 0) && (ErrorCounterLogged))
  {
    Log("ErrorCounter 0.");
    ErrorCounterLogged = false;
  }

  // if clock is not correctly adjusted in 100 seconds or motor error is read 10 times then disable motor for 500 seconds (cool down)
  if ((ErrorCounter > 3000) && ClockEnabled && !TestMode)
  {
    Log("Error counter exceeded threshold. Clock disabled.");
    ClockErrorText.concat("ErrCntrTooBig ");
    EnableMotor(false);
    ClockEnabled = false;
    ClockError = true;
  }
  if ((ErrorCounter < 10) && !ClockEnabled && !TestMode)
  {
    Log("Error counter ok. Clock enabled.");
    EnableMotor(true);
    ClockEnabled = true;
  }

  if (ErrorCounter > 10)
    ClockWarning = true;

  if (ErrorCounter > 1000)
    ClockError = true;

  if (!WifiIsConnected())
    ClockWarning = true;

  if (ClockWarning)
  {
    ClockErrorText.concat("WARNING ");
    /*
    ClockErrorText.concat("WARNING (diff = ");
    ClockErrorText.concat(round((float)delta * 60 / CPR));
    ClockErrorText.concat(" min) ");
    */
  }
  if (ClockError)
    ClockErrorText.concat("ERROR ");

  heartBeatLed++;
  if (heartBeatLed >= 10)
  {
    LEDbuiltin_Toggle(); // toggle onboard LED
    heartBeatLed = 0;
  }
}

//========================================================================================================

#ifdef MQTT_ENABLED
unsigned long lastMqttCommandExecuted = -1;
bool MqttCommandReceived = false;
#endif

void MainLoopMQTTTasks(void)
{
#ifdef MQTT_ENABLED
  MqttLoopFrequently();

  MqttCommandReceived = false;

  if (MqttCommandPowerReceived)
  {
    MqttCommandPowerReceived = false;
    LogNS("CMD: Power = %d\r\n", ConfigBgPower);
    MqttCommandReceived = true;
  }
  if (MqttCommandBrightnessReceived)
  {
    MqttCommandBrightnessReceived = false;
    LogNS("CMD: Brightness = %d\r\n", ConfigBgBrightness);
    // LED_SetDimming(MqttCommandBrightness); // system indicators have own brightness
    MqttCommandReceived = true;
  }
  if (MqttCommandColorReceived)
  {
    MqttCommandColorReceived = false;
    LogNS("CMD: RGB = 0x%6X\r\n", ConfigBgColor);
    MqttCommandReceived = true;
  }
  if (MqttCommandEffectReceived)
  {
    MqttCommandEffectReceived = false;
    LogNS("CMD: Effect = %d (%s)\r\n", ConfigBgEffectNumber, ConfigBgEffectStr.c_str());
    MqttCommandReceived = true;
  }
  if (MqttCommandEffectDurationReceived)
  {
    MqttCommandEffectDurationReceived = false;
    LogNS("CMD: Rainbow sec = %.1f\r\n", ConfigEffectDuration);
    MqttCommandReceived = true;
  }
  /*
  if (MqttCommandDotsReceived)
  {
    MqttCommandDotsReceived = false;
    LogNS("CMD: Dots = %d\r\n", MqttCommandDots);
    MqttCommandReceived = true;
  }
  */
  if (MqttCommandDotsBrightnessReceived)
  {
    MqttCommandDotsBrightnessReceived = false;
    LogNS("CMD: Dots brightness = %d\r\n", ConfigDotsBrightness);
    MqttCommandReceived = true;
  }

  if (MqttCommandReceived)
  {
    lastMqttCommandExecuted = millis();
  }

  if (((millis() - lastMqttCommandExecuted) > (MQTT_SAVE_PREFERENCES_AFTER_SEC * 1000)) && (lastMqttCommandExecuted != -1))
  {
    lastMqttCommandExecuted = -1; // this means data was saved.
    storedConfigSave();
  }

  // fill sensors
  MqttStatusTemperture = MotorTemperature;
  MqttStatusRssi = WifiGetSignalLevel();
  MqttStatusErrorCounter = ErrorCounter;
  MqttStatusErrorText = ClockErrorText;

  MqttLoopInFreeTime();
#endif
}

//========================================================================================================

void MainLoopLEDTasks(void)
{
  uint32_t LEDcolor;

  if (!HasTimeElapsed(&LastTimeLEDTaskRun, 100))
    return; // run 10x per second

  /*
  if (CurrentHour != LastHour)
  {
    if ((CurrentHour >= NIGHT_TIME) || (CurrentHour < DAY_TIME))
    {
      LED_clear(true);
      LED_SetBrigtness(0);
      return; // don't process anything else. Keep it off.
    }
    else
    {
      if (CurrentHour >= EVENING_TIME)
      {
        LED_SetBrigtness(EVENING_TIME_DIMMING);
      }
      else
      {
        LED_SetBrigtness(DAY_TIME_BRIGHTNESS);
      }
    }
    LastHour = CurrentHour;
  }
  if (LED_mustBeOff())
    return; // don't process anything else. Keep it off.
*/

  if (!ConfigBgPower)
  {
    LED_clear(false); // background off
  }
  else
  {
    // background effect
    switch (ConfigBgEffectNumber)
    {
    case 0: // Static color
      LEDcolor = ConfigBgColor;
      adjustColorBrightness(&LEDcolor, ConfigBgBrightness); // background has individually adjustable brightness; not linked to clock's brightness
      LED_allSameColor(LEDcolor, false);                    // set background
      break;

    case 1: // Uniform rainbow
      LED_EffectRainbow(8, ConfigEffectDuration, ConfigBgBrightness);
      break;

    case 2: // Travelling full rainbow
      LED_EffectRainbow(1, ConfigEffectDuration, ConfigBgBrightness);
      break;

      case 3: // Travelling partial rainbow
      LED_EffectRainbow(3, ConfigEffectDuration, ConfigBgBrightness);
      break;

      case 4: // White sparkles over configured background
      LEDcolor = ConfigBgColor;
      adjustColorBrightness(&LEDcolor, ConfigBgBrightness);
      LED_EffectTwinkleFade(LEDcolor, clWHITEbright, (uint8_t)ConfigEffectDuration);
      //LED_EffectSparkling(LEDcolor, clWHITEbright, (uint8_t)(ConfigEffectDuration / 10));
      break;

      case 5: // 
      LED_EffectTEST();
      break;

    default:
      LED_clear(false); // dark
      break;
    }
  } // power = on

  if ((ConfigDotsBrightness > 0) || ((ConfigBgBrightness > 0) && (ConfigBgPower))) // show status if not total darkness
  {
    if (ClockError)
      LEDcolor = clREDbright;
    else if (ClockWarning)
      LEDcolor = clORANGEbright;
    else if (ClockEnabled)
      LEDcolor = clBLUEdim;
    else
      LEDcolor = clPINKbright;

    adjustColorBrightness(&LEDcolor, ((ConfigDotsBrightness + ConfigBgBrightness) / 2));

    LED_showSingleDot(0.00, LEDcolor, false); // just the top one
    if (ClockError || ClockWarning)
    {
      LED_showSingleDot(0.25, LEDcolor, false);
      LED_showSingleDot(0.50, LEDcolor, false);
      LED_showSingleDot(0.75, LEDcolor, false);
    }
  }

  if (ConfigDotsBrightness > 0)
  {
    LEDcolor = SECONDS_DOT_COLOR;
    adjustColorBrightness(&LEDcolor, ConfigDotsBrightness);
    LED_showSingleDot((float)CurrentSecond / 60, LEDcolor, false);

    LEDcolor = MINUTE_DOT_COLOR;
    adjustColorBrightness(&LEDcolor, ConfigDotsBrightness);
    LED_showSingleDot((float)CurrentMinute / 60, LEDcolor, false);

    LEDcolor = HOUR_DOT_COLOR;
    adjustColorBrightness(&LEDcolor, ConfigDotsBrightness);
    LED_showSingleDot((((float)CurrentHour12 + (float)CurrentMinute / 60)) / 12, LEDcolor, false);
  }

  LED_transmitData(); // push everything to the LED strip
}

//========================================================================================================

void MainLoopBackgroundTasks(void) // called also from startup blocking errors
{
  ReceiveAndProcessSerialCommands();
  loggerPurgeToFile();
  LoopSocketServer();
  OTA_loop();
}

//========================================================================================================

void loop()
{
  MainLoopClockTasks();
  MainLoopMQTTTasks();
  MainLoopLEDTasks();
  MainLoopBackgroundTasks();
} // loop

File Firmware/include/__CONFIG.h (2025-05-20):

/*
 * Author: Aljaz Ogrin
 * Project: 
 * Hardware: ESP32
 * File description: Global configuration for the project
 */
 
#ifndef __CONFIG_H_
#define __CONFIG_H_

#include <arduino.h>
#include "____CONFIG_SECRETS.h"

// ********************* General config *********************
#define DEBUG_OUTPUT
#define DBG_SOCKET_ENABLED 1
#define DBG_SOCKET_PORT 23

#define DEVICE_NAME "WallClock" // no spaces!
#define WIFI_CONNECT_TIMEOUT_SEC 240  // How long to wait for WiFi

#define TIME_SERVER1  "si.pool.ntp.org"
#define TIME_SERVER2  "pool.ntp.org"
#define TIME_SERVER3  "time.nist.gov"
/* timezone: 
find your string here: https://github.com/nayarsystems/posix_tz_db/blob/master/zones.csv
decoding of the string: https://www.gnu.org/software/libc/manual/html_node/TZ-Variable.html
*/
#define TIMEZONE "CET-1CEST,M3.5.0,M10.5.0/3"  // Europe/Ljubljana
/*
#define DAY_TIME       6
#define EVENING_TIME  22
#define NIGHT_TIME    23
*/
// ********************* WiFi config *********************
//#define WIFI_SSID  "..." -> enter into the file __CONFIG_SECRETS.h
//#define WIFI_PASSWD "..."
#define WIFI_RETRY_CONNECTION_SEC  90


// ********************* MQTT config *********************
#define MQTT_ENABLED                     1  // enable general MQTT support
#define MQTT_SAVE_PREFERENCES_AFTER_SEC 30  // auto save config X seconds after last MQTT message received

#define MQTT_REPORT_STATUS_EVERY_SEC    60  // report status to MQTT every X seconds
#define MQTT_RECONNECT_WAIT_SEC        120  // wait X seconds before trying to reconnect to MQTT broker

#define MQTT_RETAIN_STATE_MESSAGES      false  // https://www.home-assistant.io/integrations/mqtt/#using-retained-state-messages

#define MQTT_ALIVE_TOPIC             "connection" // availability_topic :: https://www.home-assistant.io/integrations/mqtt/#availability_topic
#define MQTT_ALIVE_MSG_ONLINE        "online"     // default in HA. If changed, configure "payload_available" and "payload_not_available"
#define MQTT_ALIVE_MSG_OFFLINE       "offline"
#define MQTT_RETAIN_ALIVE_MESSAGES   false

// --- MQTT Home Assistant settings ---
// You will either need a local MQTT broker to use MQTT with Home Assistant (e.g. Mosquitto) or use an internet-based broker with Home Assistant support.
// If not done already, you can set up a local one easily via an Add-On in HA. See: https://www.home-assistant.io/integrations/mqtt/
// Enter the credential data into the MQTT broker settings section below accordingly.

#define MQTT_HOME_ASSISTANT_DISCOVERY                     1             // Uncomment if you want HA auto-discovery
#define MQTT_RETAIN_DISCOVERY_MESSAGES                    false         // https://www.home-assistant.io/integrations/mqtt/#discovery-messages-and-availability
// retain discovery = true:  Configuration is stored in the MQTT broker. HA directly responds to the existing messages. Configuration can be deleted on the MQTT broker (use MQTT Explorer program).  Restart of the broker, device or HA does not clear the config.
// retain discovery = false: Configuration is stored in the HA and can be deleted in Settings -> Devices -> MQTT. Restart of the broker, device or HA does not clear the config.
#define MQTT_HOME_ASSISTANT_DISCOVERY_DEVICE_MANUFACTURER "Aljaz"       // Name of the manufacturer shown in HA
#define MQTT_HOME_ASSISTANT_DISCOVERY_DEVICE_MODEL        DEVICE_NAME   // Name of the model shown in HA
//#define MQTT_HOME_ASSISTANT_DISCOVERY_SW_VERSION          VERSION       // Firmware version shown in HA
#define MQTT_HOME_ASSISTANT_DISCOVERY_HW_VERSION          "1.0"         // Hardware version shown in HA

// --- MQTT broker settings ---
/*  -> enter into the file __CONFIG_SECRETS.h
#define MQTT_BROKER    ...                    // Broker host
#define MQTT_PORT      1883                   // Broker port
#define MQTT_USERNAME  ...                    // Username
#define MQTT_PASSWORD  ...                    // Password
*/
#define MQTT_CLIENT    DEVICE_NAME            // Device Id 
// #define MQTT_USE_TLS                                 // Use TLS for MQTT connection. Setting a root CA certificate is needed!
                                                     // Don't forget to copy the correct certificate file into the 'data' folder and rename it to mqtt-ca-root.pem!
                                                     // Example CA cert (Let's Encrypt CA cert) can be found in the 'data - other graphics' subfolder in the root of this repo

// ********************* Hardware *********************
  
#ifdef FREE_JTAG_PINS
  #define TFT_CS        0
  #define TFT_SCLK      0
  #define TFT_MISO      0
  #define TFT_MOSI      0
#else
  #define TFT_CS        15  // JTAG !!
  #define TFT_SCLK      14  // JTAG !!
  #define TFT_MISO      12  // JTAG !!
  #define TFT_MOSI      13  // JTAG !!
#endif

// ********************* Motor *********************

// Pin definitions
#define nSTBY_nRESET_PIN   GPIO_NUM_21
//#define nBUSY_PIN          not connected
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

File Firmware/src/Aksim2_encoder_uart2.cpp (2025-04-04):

#include <Arduino.h>
#include <stdint.h>
#include "__CONFIG.h"
#include "Logger.h"
#include "Aksim2_encoder_uart2.h"

uint8_t RxBuffer[1 + 58];
String dbgStr;

uint32_t EncoderPosST;
int16_t EncoderPosMT;
bool EncoderWarning, EncoderError;
uint16_t EncoderDetailedStatus;
uint16_t EncoderSignalLevel;
float EncoderAirGap;

bool queryEncoder(uint8_t command, uint8_t DataLength, bool printData)
{
    while (Serial2.available())
        Serial2.read(RxBuffer, 1); // clear rx buffer

    // unsigned long startTime = millis();
    Serial2.write(command);
    memset(RxBuffer, 0x00, sizeof(RxBuffer));
    if (command == 'v')
        delay(20);
    else
        delay(2);
    uint8_t bytesRead;
    // log_i("Encoder data available: %d", Serial2.available());
    bytesRead = Serial2.read(RxBuffer, 1 + DataLength);
    //    log_i("Encoder read bytes: %d; TRX duration: %d ms", bytesRead, millis() - startTime);

    if (printData)
    {
        dbgStr.clear();
        for (int i = 0; i < bytesRead; i++)
        {
            dbgStr.concat("%2X ", RxBuffer[i]);
        }
        LogNS("Data: %s\r\n", dbgStr.c_str());
    }

    if (command == 'v')
    {
        dbgStr.clear();
        for (int i = 0; i < bytesRead; i++)
        {
            char ch = (char)RxBuffer[i];
            if ((ch >= '!') && (ch <= 'z'))
                dbgStr.concat(ch);
        }
        dbgStr.trim();
        LogNS("Data: %s \r\n", dbgStr.c_str());
    }
    return (bytesRead == (DataLength + 1));
}

bool encoderInit(void)
{
    bool result = false;
    Log("Encoder init...");
    Serial2.begin(115200, SERIAL_8N1, RXD2pin, TXD2pin);
    delay(20);
    Serial2.flush();
    Serial2.setTimeout(300); // max 0.3 sec
    /*
    [  3382][I][Aksim2_encoder_uart2.cpp:55] encoderRead(): Encoder read bytes: 59
    [  3389][I][Aksim2_encoder_uart2.cpp:56] encoderRead(): Read duration: 12 ms
    Data: vAksIM-2URA_01MB029SFA17MFNT00'!----------------
    Data: 76 41 6B 73 49 4D 2D 32 20 55 52 41 5F 30 31 20 20 20 4D 42 30 32 39 53 46 41 31 37 4D 46 4E 54 30 30 20  2  9  3  0  0 27 21 20 2D 2D 2D 2D 2D 2D 2D 2D 2D 2D 2D 2D 2D 2D 2D 2D
    */
    if (queryEncoder('v', 58, true))
    {
        int idx = dbgStr.indexOf("MB029SFA17MFNT00");
        if (idx > 0)
        {
            Log("Encoder found and data is correct.");
            if (encoderRead(true))
            {
                result = !EncoderError;
            }
        }
        else
        {
            Log("Encoder didn't return correct identification! idx = %d", idx);
        }
    }
    else
    {
        Log("No useful data returned from encoder!");
    }
    return result;
}

bool encoderRead(bool PrintData)
{
    bool result = false;
    if (queryEncoder('d', 7, false)) // detailed status
    {
        if (RxBuffer[0] == 'd')
        {
            // endiannness is incorrect, can't use memcpy...
            EncoderPosMT = (RxBuffer[1] << 8) | RxBuffer[2];
            EncoderPosST = (RxBuffer[3] << 24) | (RxBuffer[4] << 16) | RxBuffer[5];
            EncoderDetailedStatus = (RxBuffer[6] << 8) | RxBuffer[7];

            EncoderError = !(EncoderPosST & 0x0002);
            EncoderWarning = !(EncoderPosST & 0x0001);
            EncoderPosST = EncoderPosST >> (32 - 17); // align LSB of the position and cut status bits

            if ((EncoderDetailedStatus != 0) || PrintData)
            {
                Log("Encoder: MT = %d; ST = %d; E = %d; W = %d;  status = 0x%4X.", EncoderPosMT, EncoderPosST, EncoderError, EncoderWarning, EncoderDetailedStatus);
                String sDetStatus;
                sDetStatus.clear();
                if ((EncoderDetailedStatus & 0x8000) > 0)
                    sDetStatus.concat("Multiturn error  ");
                if ((EncoderDetailedStatus & 0x4000) > 0)
                    sDetStatus.concat("Signal clipping error  ");
                if ((EncoderDetailedStatus & 0x2000) > 0)
                    sDetStatus.concat("Signal clipping warning  ");
                if ((EncoderDetailedStatus & 0x1000) > 0)
                    sDetStatus.concat("Sensor error  ");
                if ((EncoderDetailedStatus & 0x0800) > 0)
                    sDetStatus.concat("Sensor read error  ");
                if ((EncoderDetailedStatus & 0x0400) > 0)
                    sDetStatus.concat("Config error  ");
                if ((EncoderDetailedStatus & 0x0080) > 0)
                    sDetStatus.concat("Signal high warning  ");
                if ((EncoderDetailedStatus & 0x0040) > 0)
                    sDetStatus.concat("Signal low warning  ");
                if ((EncoderDetailedStatus & 0x0020) > 0)
                    sDetStatus.concat("Signal lost error  ");
                if ((EncoderDetailedStatus & 0x0010) > 0)
                    sDetStatus.concat("Temperature warning  ");
                if ((EncoderDetailedStatus & 0x0008) > 0)
                    sDetStatus.concat("Supply error  ");
                if ((EncoderDetailedStatus & 0x0004) > 0)
                    sDetStatus.concat("System error  ");
                if ((EncoderDetailedStatus & 0x0002) > 0)
                    sDetStatus.concat("Magnetic error  ");
                if ((EncoderDetailedStatus & 0x0001) > 0)
                    sDetStatus.concat("Acceleration error  ");
                if (sDetStatus.length() > 2)
                    Log("Encoder status:  %s.", sDetStatus.c_str());
            }
            result = true; // !EncoderError is handled elsewhere
        }
        else
        {
            Log("Incorrect header returned!");
        }
    }
    else
    {
        Log("No useful data returned from encoder!");
    }
    return result;
}

bool encoderReadAirGap(void)
{
    bool result = false;
    if (queryEncoder('a', 7, false)) // signal level
    {
        if (RxBuffer[0] == 'a')
        {
            // endiannness is incorrect, can't use memcpy...
            EncoderPosMT = (RxBuffer[1] << 8) | RxBuffer[2];
            EncoderPosST = (RxBuffer[3] << 24) | (RxBuffer[4] << 16) | RxBuffer[5];
            EncoderSignalLevel = (RxBuffer[6] << 8) | RxBuffer[7];

            EncoderError = !(EncoderPosST & 0x0002);
            EncoderWarning = !(EncoderPosST & 0x0001);
            EncoderPosST = EncoderPosST >> (32 - 17); // align LSB of the position and cut signal level

            if (EncoderSignalLevel > 0)
                EncoderAirGap = -95.49 * log(EncoderSignalLevel) + 977.0; // K × Ln (SignalLevel) + N
            else
                EncoderAirGap = 0;

            Log("Encoder: MT = %d; ST = %d; E = %d; W = %d;  SignalLevel = %u; Air gap = %.1f um", EncoderPosMT, EncoderPosST, EncoderError, EncoderWarning, EncoderSignalLevel, EncoderAirGap);
            result = true; // !EncoderError is handled elsewhere
        }
        else
        {
            Log("Incorrect header returned!");
        }
    }
    else
    {
        Log("No useful data returned from encoder!");
    }
    return result;
}
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

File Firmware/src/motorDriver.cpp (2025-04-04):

#include <Arduino.h>
#include <Ponoor_PowerSTEP01Library.h>
#include <SPI.h>
#include "__CONFIG.h"
#include "motorDriver.h"
#include "Logger.h"


SPIClass myVSPI (VSPI);

// powerSTEP library instance, parameters are distance from the end of a daisy-chain
// of drivers, !CS pin, !STBY/!Reset pin, !Busy pin (optional)
powerSTEP driver(0, VSPI_nCS, nSTBY_nRESET_PIN);  // Busy not configured -> reads from the register over SPI
//powerSTEP driver(0, VSPI_nCS, nSTBY_nRESET_PIN, nBUSY_PIN);

bool HiPowerMode;

bool MotorInit() 
{
  bool result = false;
  Log("powerSTEP01 control initialising...");

  // Library does not initialize pins - let's do it here.
  pinMode(nSTBY_nRESET_PIN, OUTPUT);
  //pinMode(nBUSY_PIN, INPUT);  
  pinMode(VSPI_nCS, OUTPUT);


  // Reset powerSTEP and set CS
  digitalWrite(VSPI_nCS, HIGH);
  digitalWrite(nSTBY_nRESET_PIN, HIGH);
  delay(50);
  digitalWrite(nSTBY_nRESET_PIN, LOW);
  delay(50);
  digitalWrite(nSTBY_nRESET_PIN, HIGH);

  // Start SPI
  myVSPI.begin(VSPI_SCK, VSPI_MISO, VSPI_MOSI, VSPI_nCS);
  myVSPI.setFrequency(100000); // 100 kHz
  myVSPI.setDataMode(SPI_MODE3); // configure CPOL and CPHA

  // Configure powerSTEP
  driver.SPIPortConnect(&myVSPI); // give library the SPI port

  Log("Testing comm...");
  Log("Status = 0x%4X", driver.getStatus());

  byte bOCT = driver.getOCThreshold();
  Log("OC Threshold = %d (must be 8 after reset)", bOCT);
  if (bOCT == 8)  // must be 8 after reset
  {
    Log("Communication is ok.");
    result = true;
  }
  else
  {
    Log("Communication is NOT GOOD!!");
    result = false;
  }

  // Programmable UVLO thresholds
  unsigned long configVal = driver.getParam(CONFIG);
  // This bit is CONFIG 8, mask is 0x0100
  configVal &= ~(0x0100); // reset the bit for low voltage operation
  driver.setParam(CONFIG, configVal);
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

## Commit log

2025-02-10 Added documentation
    [NTCALUG01T103G.STEP, Typical config.xlsx, VoltageParametriZaMotorje.xlsx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]
2025-02-10 Added 3D files
    [MB029xxxxxxFNx00.STEP, MRA029BC010DSE00.STEP, NTCALUG01T103G.STEP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]
2025-02-10 Added firmware
    [Hardware pinout.xlsx, partition_noOta_1Mapp_3Mspiffs.csv]
2025-02-14 Reading air gap of encoder.
2025-02-16 Added Over The Air update (OTA)
    [partition_1Mapp_OTA_2Mfs.csv]
2025-02-16 encoder connection diagram
2025-02-16 Longer LED strip
2025-02-17 LED strip tuning.
2025-02-18 Tune LED colors, process commands on blocked startup.
2025-02-19 Clock position loop, esp reset reason.
    [Clock.cpp, SerialCommands.cpp, __CONFIG.h]
2025-02-19 Added 3D print build files
    [0.stl, 1.stl, 2.stl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]
2025-02-20 Backup 3D files
    [pokrov elektronike.stl]
2025-02-24 Global error and warning bits.
    [Aksim2_encoder_uart2.cpp, Clock.cpp, LEDs.cpp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]
2025-02-24 Additional designs.
    [dust protector.stl, hand 1 M a v61.stl, hand 1 M b v61.stl]
2025-03-19 added 3D dust cover
    [dust protector 2.stl, pokrov elektronike 2.stl]
2025-03-24 LED timing copied from FastLED library
2025-03-25 Added device class
2025-03-29 Updated images and 3D design
    [full_clock_v68.f3z, mechanism_v101.f3z, stenska ura v31.f3z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]
2025-05-20 Fix too frequent mqtt reconnect
    [Mqtt_client_HA.cpp, __CONFIG.h, main.cpp]
2026-03-14 Updated HA Discovery; fixed temperature unit
    [Mqtt_client_HA.cpp]
